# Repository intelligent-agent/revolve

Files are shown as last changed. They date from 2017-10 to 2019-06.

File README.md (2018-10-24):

```
    _/_/_/                                    _/                       
   _/    _/    _/_/    _/      _/    _/_/    _/  _/      _/    _/_/    
  _/_/_/    _/_/_/_/  _/      _/  _/    _/  _/  _/      _/  _/_/_/_/   
 _/    _/  _/          _/  _/    _/    _/  _/    _/  _/    _/          
_/    _/    _/_/_/      _/        _/_/    _/      _/        _/_/_/     
                                                                       
```                                                                      

## Main features
- 1GHz Single board solution using [Octavo OSB3358 SIP](https://octavosystems.com/2016/05/09/osd3358-new-era-integration/)
- 6 [TMC2130](https://www.trinamic.com/products/integrated-circuits/details/tmc2130/) stepper drivers, stall detection, overcurrent/temp
- 4 Thermistor or Thermocouple inputs (runtime configurable)
- 4 high power heater outputs
- 4 GB fast eMMC
- Optionally 2 external drivers
- [Direct coupled PRU lines](http://beagleboard.org/pru) to all drivers
- Flexible PWM on all 8 MOSFET outputs for flexible EMC passing
- 4 USB host ports, 1 USB device port
- 10/100Mbit Ethernet
- 1080p HDMI
- Smart power controls
 - Input voltage and current measurement
 - Power removed detection
 - Software defined overcurrent protecion
- Quad encoder input for filament sensor
- Buffered end stop inputs, ESD protected connectors
- 2 Servo outputs
- Inductive sensor input
- Two Grove connectors, I2C and UART

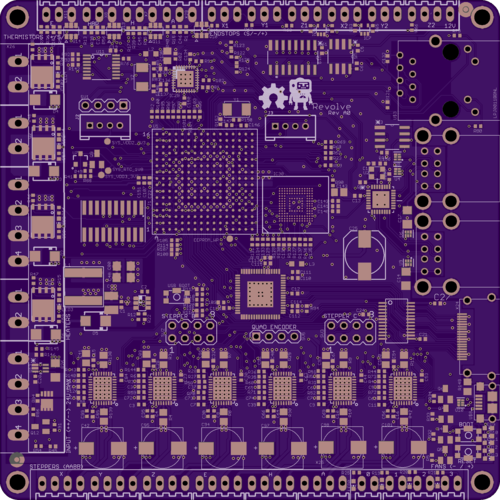
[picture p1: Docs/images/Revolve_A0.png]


## Power management
Here is an overview of the power distribution


## 5V step down TPS54202 calculations

```python
import math
Vout = 5.1 # Output voltage
Vin = 24 # Input voltage
Iout = 2 # Output current
Kind = 0.3 # ?
Fsw = 500000 # Switching frequency
Cbulk = 10 *10**-6
u = 10**6 # micro

```

```python
L=(Vout*(Vin-Vout))/(Vin*Kind*Iout*Fsw)
print "Inductor selection:"
print "Minimum inductor size: "+str(L*10**6)+" uH"

Lout = 15*10**-6
Ilmax = math.sqrt(Iout**2 + (1/12) + ((Vout*(Vin-Vout))/(Vin*Lout*Fsw*0.8))**2)
print "RMS Inductor current "+str(Ilmax)
Ipeak = Iout + (Vout * (Vin - Vout))/(1.6*Vin*Lout*Fsw)
print "Max inductor current "+str(Ipeak)
print "Choosing NR8040T330M"

```

    Inductor selection:
    Minimum inductor size: 13.3875 uH
    RMS Inductor current 2.10904312204
    Max inductor current 2.3346875
    Choosing NR8040T330M

```python
dIout = 0.7
dVout = 0.2 # Delta voltage with dI
Vr = 0.03 # Ripple Voltage
Ir = Iout*0.3
CO1 = (2*dIout)/(Fsw*dVout)
CO2 = (1.0/(8.0*Fsw))*(1.0/(Vr/Ir))
#CO3 =
print "Input Capacitor Selection:"
print "CO1: "+str(CO1*u) + " uF"
print "CO2: "+str(CO2*u) + " uF"

#print "Minimum capacitance: "+str(CO*u)+" uF"
print "Choosing 20uF"
```

    Input Capacitor Selection:
    CO1: 14.0 uF
    CO2: 5.0 uF
    Choosing 20uF

```python
R2 = 100.0*10**3
R3 = 13.3*10**3
Vref = 0.596
Vout = Vref*((R2/R3)+1)
print "Calculation of output resistance: "
print "Vout = "+str(Vout)
```

    Calculation of output resistance:
    Vout = 5.07720300752

## Stepper drivers

Current sense resistor:

```python
R = 0.1
I = 1
U = R*I
P = U*I
print "Power dissipation: "+str(P)
```

    Power dissipation: 0.1

**Diagnostics:**
```python
$2*8 = 16$
```

* Connect together to form a single interrupt?
No, it's good to have individual pins for stallguard.

## Capacitor selection
- 100uF electrolytic capacitor is recommended. No mention of ESR or ripple current in the TMC2130 data sheet.
- What is the frequency at which the largest current draw is expected?
- There are 10uF capacitors in line to handle high frequency current draws, so it is expected that the electrolytic capacitors will handle lower frequecy draws. It depends on cable length, ESR in PSU as well.

**SPI and enable**  
* Enable pins, can it be done using SPI?
* SPI CS pins, need 8 pins at least.
    * Use Mux?
        * Increased cost. How much?
        *
    * Daisy chain?
        * What is the required time?
        * Not good for Stepper A/B. Use CN1?
        * Each transaction takes 60 us
    * Individual pins.
        * Requires 8 pins.
*

```python
print "Stepper readout time: "
a = 6.0*40/(4*10**6)
print "it takes "+str(a*u)+" us for each transaction"
```

    Stepper readout time:
    it takes 60.0 us for each transaction

## PWM calculations

**Current setting**
* Use PWM chip?
    * Costly > $1
    * board space
* Use internal reference
    * 5 bit precision

```python
print "Number of current steps on TMC2130: "+str(2**5)
```

    Number of current steps on TMC2130: 32

# Smart input current monitor circuit.
Fuses have slow responses, so they do not protect against short circuits
and only asymptotically approach their rating with time. They are temperature dependent, difficult to
replace, and physically large. They also increase manufacturing time and cost due to almost universally being
through-hole components.

 - Measure input voltage
 - Measure input current.
 - Choosing PMOS to also implement power lost detection.
 - Reverse polarity protection

```python
R = 0.001
A = 30
adc_vals = 2**12
v_adc = 1.8
v_res = R*A
Gain = 50
resolution =(v_adc/adc_vals)/R/Gain

print "Over current calculations:"
print "Max current: "+str(A)+" A"
print "Resistor value: "+str(R*1000)+" mOhm"
print "Voltage drop across resistor: "+str(v_res*1000)+" mV"
print "Voltage measured: "+str(v_res*Gain)
print "Power dissipation in Rsense: "+str(R*A*A)+" W"
print "resolution: "+str(resolution*1000)+" mA"
```

    Over current calculations:
    Max current: 30 A
    Resistor value: 1.0 mOhm
    Voltage drop across resistor: 30.0 mV
    Voltage measured: 1.5
    Power dissipation in Rsense: 0.9 W
    resolution: 8.7890625 mA

```python
v_max = 24
R1 = 100*10**3
R2 = 4.7*10**3
print "Input voltage calculations: "
print "Voltage divider max output: "+str(v_max*R2/(R1+R2))
print "Input voltage resolution: ??"
```

    Input voltage calculations:
    Voltage divider max output: 1.07736389685
    Input voltage resolution: ??

```python
Imax = 30
RDS = 5.6*10**-3
Ploss = RDS*Imax*Imax
print "Input P-mos power calculations:"
print "Power expenditure: "+str(Ploss)+ " W"
```

    Input P-mos power calculations:
    Power expenditure: 5.04 W

## ESD considerations
 - EN 55024/EN 61000-4-2: ±4kV Contact, ±8kV Air
### Board
 - Ground shield, having 0.1R to ground.
### USB
 - Using [TPD4S012](http://www.ti.com/product/TPD4S012) having Contact: ±10kV, Air: ±10kV
### HDMI
 - Using [TPD12S016](http://www.ti.com/product/TPD12S016)
### Ethernet
 - Isolated using magnetics.
### Endstops
 - Input buffer [CD4050BD](http://www.ti.com/product/CD4050BD) with HBD: ±1500, CDM: ±1000
### Analog
 - Series resistance
### Steppers
 - TMC2130 HBM: ±4 kV
### Heater MOSFETs
 - 4.7nF protection
### Fan MOSFETS
 - No protection

## Layout considerations
Using en562748 as reference for PHY layout.
 - Using 100R resistors in series to reduce EMI.
 - Placing PHY chip close to SIP since differential lines radiate less than 3.3V single ended lines.
 - Removing ground plane under magnetics.
 - 100 Ohm differential impedance
 - Place 49.9ohm pullups close to PHY chip.
 - OSH park uses FR408 laminate

```python
Er = 3.67 # Relative dielectric costant
H = 0.17018 # prepreg height in mm
T = 0.035 # Copper thickness (mm)
F = 125 # Frequency MHz
print "0.15/0.15 track and gap gives 98.4 differential and 65.3 single ended"
```

    0.15/0.15 track and gap gives 98.4 differential and 65.3 single ended

```python
Vf = 2.8 # Diode forward voltage drop (V)
Vin = 3.3 # Input voltage (V)
Vres = Vin-Vf
If = 0.0001 # Diode current, 1mA
R = Vres/If
print "LED power calculations: "
print "Resistor for {}, {}mA: {}".format(Vin, If*1000,R)
```

    LED power calculations:
    Resistor for 3.3, 0.1mA: 5000.0

# Sysboot config
Two Boot modes: MMC1 or USB device
 - SYSBOOT[15-14] = 10b = 25MHz
 - SYSBOOT[13:12] = 00b = reserved
 - SYSBOOT[11:10] = xx
 - SYSBOOT[9] = xx
 - SYSBOOT[8] = xx
 - SYSBOOT[7-6] = xx
 - SYSBOOT[5] = 0b = Disable CLKOUT1
 - SYSBOOT[4:0] = 11100b = MMC1, MMC0, UART0, USB0

 To boot from USB:
 - SYSBOOT[4:0] = 11000b = SPI0, MMCO0, USB0, UART0

```python
Imax = 1.5 # Maximum output current on all 4 USB ports
Rmeas = 0.01 # Current measurement resistor on low side.
RDSon = 0.065 #P-mos RDSon
Vin = 5.1
Vdrop = Vin - (Rmeas + RDSon)*Imax
print "Voltage drop across R: {}".format(Rmeas*Imax)
print "Resulting voltage to USB: {}".format(Vdrop)
```

    Voltage drop across R: 0.015
    Resulting voltage to USB: 4.9875

```python
Imax = 1.5 # Maximum output current on all 4 USB ports
Rmeas = 0.01 # Current measurement resistor on low side.
RDSon = 0.065 #P-mos RDSon
Vin = 5.1
Vdrop = Vin - (Rmeas + RDSon)*Imax
print "Voltage drop across R: {}".format(Rmeas*Imax)
print "Resulting voltage to USB: {}".format(Vdrop)
```

    Voltage drop across R: 0.015
    Resulting voltage to USB: 4.9875

### Review
 - Changed vias to tented
 - Moved pin 1 indicator on U2
 - Moved all test points to top side
 -

```python
from IPython.display import display, Markdown, Latex
```

## Calculation of power dissipation of P-MOS
* `$R_{ds(on)max} = 45 m\Omega$ @ $-10 V$`
* Thermal Resistance, Junction to Ambient @ `$TA=+25 ^{\circ}C$ is $R_{\theta JA}=26 ^{\circ}C/W$`

```python
Von=6
Ta=25
Imax=30
#Imax=2
Rdson=0.0045
TR=26

# P=I^2*R
P=Imax*Imax*Rdson

Trise=TR*P
T=Ta+Trise

display(Markdown("""
$P={P:0.3f} W$\n
$T_{{rise}} = {Trise} ^{{\circ}}C$\n
$T = T_A + T_{{rise}} = {T:0.3f} ^{{\circ}}C$ when $I={I:.0f} A$

""".format(P=P, Trise=Trise, T=T, I=Imax)))
```

    $P=4.050 W$

    $T_{rise} = 105.3 ^{\circ}C$

    $T = T_A + T_{rise} = 130.300 ^{\circ}C$ when $I=30 A$

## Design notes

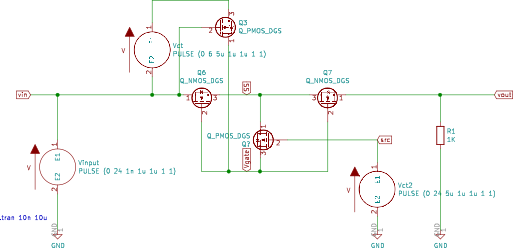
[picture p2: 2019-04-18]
PCB/Revolve_A5/img/schematic.png

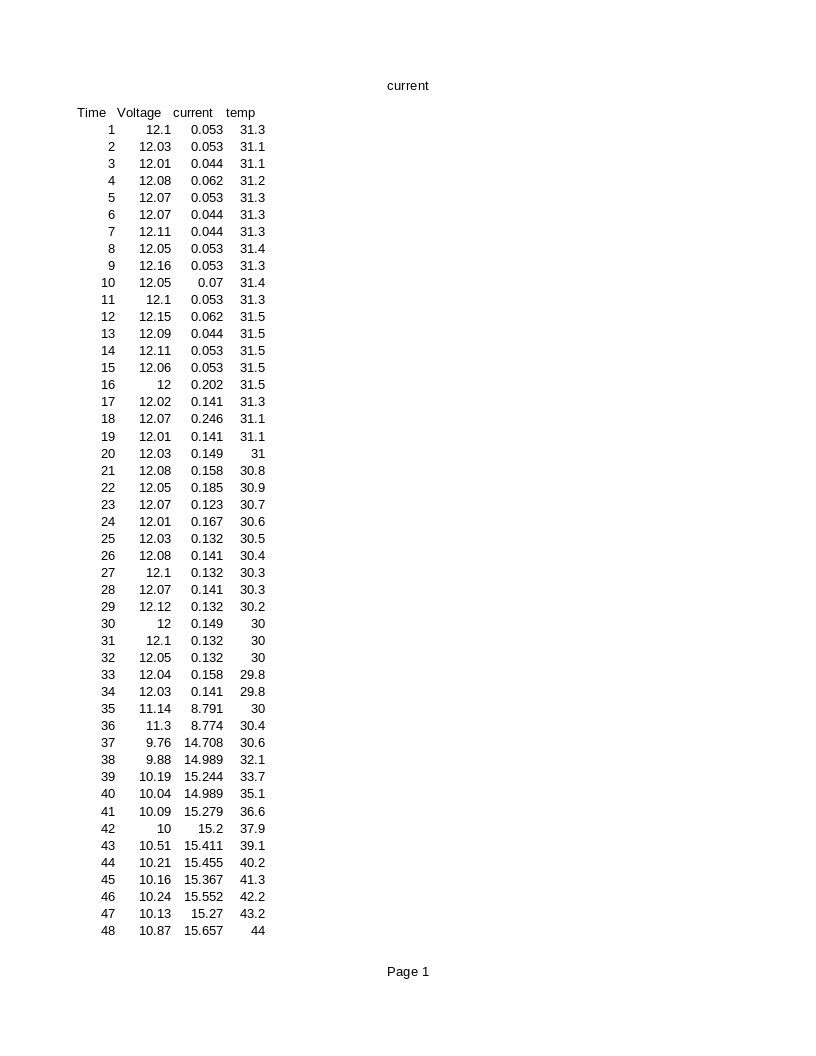
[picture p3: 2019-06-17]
PCB/Revolve_A5/img/current_15A_fan.png

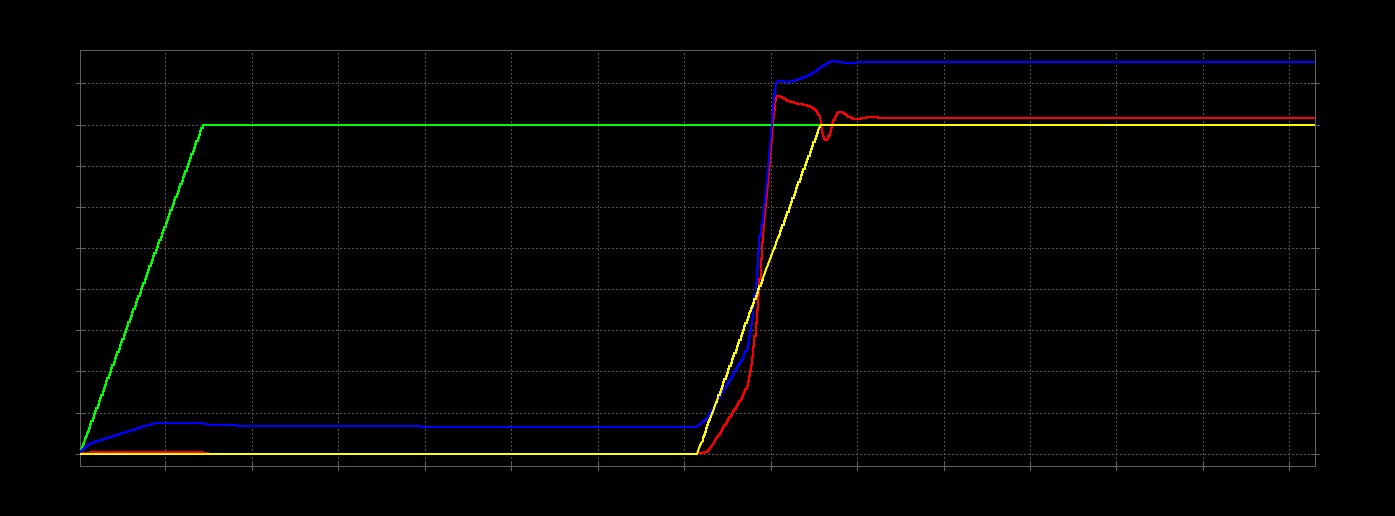
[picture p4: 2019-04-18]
PCB/Revolve_A5/img/simulation_nmos_1R-load.png

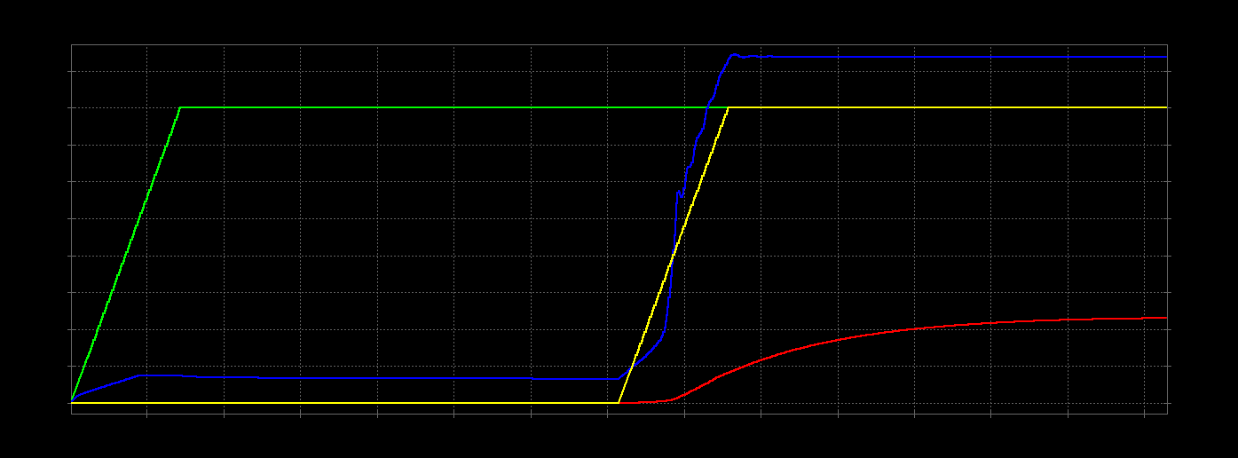
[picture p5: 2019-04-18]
PCB/Revolve_A5/img/simulation_nmos_1m-load.png

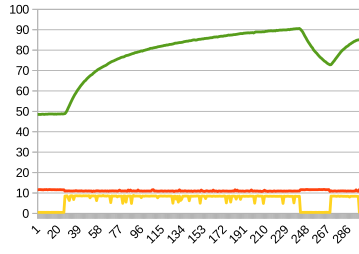
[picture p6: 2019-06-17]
PCB/Revolve_A5/img/current.png

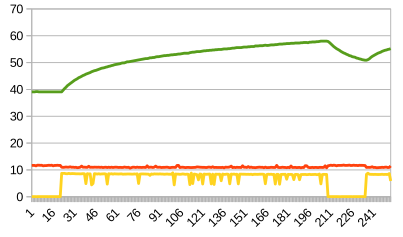
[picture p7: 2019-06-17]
PCB/Revolve_A5/img/current_new_2.png

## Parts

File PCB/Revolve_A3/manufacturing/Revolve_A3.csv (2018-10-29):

Qty | Value | Device | Package | Parts | Description | MPN | Notes
1 |  | CTI-JTAG | CTI-JTAG | J1 |  |  | DNP
2 |  | MA04-1 | MA04-1 | SV1, SV5 | PIN HEADER |  | DNP
2 |  | MA05-2 | MA05-2 | SV4, SV6 | PIN HEADER |  | DNP
5 |  | NPN-TRANSISTOR_SOT23 | SOT23 | Q4, Q5, Q6, Q7, Q12 | NPN TRANSISTOR | AO7400
1 | 0.001,1% | R-EU_R1206 | R1206 | R26 | RESISTOR, European symbol | CSR1206-0R001F1
13 | 0.1R | R-EU_R0805 | R0805 | R3, R4, R7, R8, R9, R10, R11, R29, R30, R42, R138, R139, R149 | RESISTOR, European symbol | RL1220S-R10-F
61 | 0.1uF | C-EUC0402 | C0402 | C1, C2, C4, C5, C6, C8, C10, C12, C13, C15, C16, C18, C19, C20, C21, C23, C24, C27, C28, C29, C30, C31, C35, C38, C40, C43, C44, C53, C54, C56, C60, C61, C63, C64, C66, C67, C69, C70, C72, C73, C74, C82, C83, C84, C85, C87, C99, C107, C108, C110, C114, C115, C133, C134, C138, C140, C141, C142, C150, C151, C155 | CAPACITOR, European symbol | CL10B104KB8NNND
1 | 0.1uF | C-EUC0402 | C0402 | C32 | CAPACITOR, European symbol | CL10B104KB8NNND
1 | 10,1% | R-EU_R0402 | R0402 | R83 | RESISTOR, European symbol | RC0402FR-0710RL
15 | 100 | R-EU_R0402 | R0402 | R85, R95, R96, R97, R98, R99, R100, R101, R102, R103, R104, R161, R162, R180, R181 | RESISTOR, European symbol | RC0402FR-07100RL
19 | 100K,1% | R-EU_R0402 | R0402 | R12, R45, R87, R105, R107, R108, R114, R115, R116, R117, R118, R119, R120, R174, R175, R176, R177, R178, R179 | RESISTOR, European symbol | RC0402FR-07100KL
1 | 100K,1% | R-EU_R0402 | R0402 | R84 | RESISTOR, European symbol | RC0402FR-07100KL
1 | 100uF | CPOL-EU153CLV-0605 | 153CLV-0605 | C25 | POLARIZED CAPACITOR, European symbol | RSL0J101MCN1GB
6 | 100uF,35V,0.025R | C | RHS1V10MCN1GS | C42, C94, C95, C97, C98, C101 |  | RHS1V101MCN1GS
39 | 10K,1% | R-EU_R0402 | R0402 | R1, R2, R6, R27, R31, R35, R37, R38, R39, R40, R43, R50, R55, R56, R57, R58, R60, R73, R78, R81, R88, R90, R94, R121, R127, R128, R129, R130, R131, R132, R133, R134, R135, R136, R137, R140, R141, R147, R152 | RESISTOR, European symbol | RC0402FR-0710KL
2 | 10uF,3.3V | C-EUC0805 | C0805 | C135, C143 | CAPACITOR, European symbol | C0805C106K8PACTU
7 | 10uF,35V | C-EUC0805 | C0805 | C41, C47, C89, C91, C92, C93, C100 | CAPACITOR, European symbol | GMK325BJ106MN-T | Alternative component: GRM21BR6YA106KE43K
1 | 12.1K, 1% | R-EU_R0402 | R0402 | R82 | RESISTOR, European symbol | RC0402FR-0712K1L
1 | 13.3K,1% | R-EU_R0402 | R0402 | R22 | RESISTOR, European symbol | RC0402FR-0713K3L
2 | 150OHM,800mA | L-USL2012C | L2012C | L2, L3 | INDUCTOR, American symbol | MU2029-151Y
1 | 15uH | RT8040T330 | NR8040T330 | L1 |  | NRS8040T150MJGJ
7 | 18pF | C-EUC0402 | C0402 | C36, C146, C147, C148, C149, C156, C157 | CAPACITOR, European symbol | GRM0335C1E180JA01D
1 | 1K,1% | R-EU_R0402 | R0402 | R53 | RESISTOR, European symbol | RC0402FR-071KL
7 | 1K,1% | R-EU_R0402 | R0402 | R106, R109, R110, R111, R153, R154, R155 | RESISTOR, European symbol | RC0402FR-071KL
1 | 1M | R-EU_R0402 | R0402 | R150 | RESISTOR, European symbol | RC0402JR-071ML
6 | 2.2R | R-EU_R0402 | R0402 | R52, R59, R70, R71, R72, R126 | RESISTOR, European symbol | RC0402FR-072R2L
5 | 2.2uF | C-EUC0402 | C0402 | C34, C109, C111, C112, C113 | CAPACITOR, European symbol | GRM155R61A225KE95D
4 | 22-05-7028-02 | 22-05-7028-02 | 7395-02 | X4, X5, X6, X9 | CONNECTOR | 640455-2
9 | 22-05-7038-03 | 22-05-7038-03 | 7395-03 | X1, X7, X8, X10, X11, X13, X19, X22, X29 | CONNECTOR | 640455-3
7 | 22-05-7048-04 | 22-05-7048-04 | 7395-04 | X12, X14, X15, X16, X17, X18, X25 | CONNECTOR | 640455-4
7 | 22nF | C-EUC0402 | C0402 | C3, C7, C9, C11, C39, C88, C132 | CAPACITOR, European symbol | C1005X7R1E223K050BB
4 | 22uF | C-EUC1206 | C1206 | C14, C17, C48, C80 | CAPACITOR, European symbol | CL31B106KAHNNNE
2 | 25MHz | 445C33D24M00000SMALL | 445C33D24M00000 | Y1, Y2 |  | 445C33D25M00000
49 | 4.7K,1% | R-EU_R0402 | R0402 | R5, R13, R14, R15, R16, R17, R18, R19, R20, R21, R23, R24, R25, R28, R32, R33, R34, R36, R44, R46, R47, R48, R51, R54, R61, R62, R63, R64, R65, R66, R67, R68, R69, R74, R75, R76, R77, R89, R91, R92, R93, R112, R142, R143, R144, R145, R171, R172, R173 | RESISTOR, European symbol | RC0402FR-074K7L
5 | 4.7nF | C-EUC0402 | C0402 | C22, C57, C58, C59, C102 | CAPACITOR, European symbol | CL05B472KA5NNNC
11 | 4.7uF | C-EUC0402 | C0402 | C26, C33, C37, C45, C46, C49, C55, C65, C68, C86, C103 | CAPACITOR, European symbol | GRM155R60J475ME47D
3 | 40.2K,1% | R-EU_R0402 | R0402 | R41, R86, R148 | RESISTOR, European symbol | RC0402FR-0740K2L
1 | 445C33D24M000003.2X2.5 | 445C33D24M000003.2X2.5 | 403C35E12M00000 | U$22 |  | ABM8G-12.000MHZ-4Y-T3
2 | 470 | R-EU_R0402 | R0402 | R79, R80 | RESISTOR, European symbol | RC0402JR-07470RL
1 | 470pF | C-EUC0402 | C0402 | C136 | CAPACITOR, European symbol | CL05B471KB5NNNC
1 | 47k,NTC | R-EU_R0402 | R0402 | R146 | RESISTOR, European symbol | NCP15WB473E03RC
4 | 49.9,1% | R-EU_R0402 | R0402 | R122, R123, R124, R125 | RESISTOR, European symbol | RC0402FR-0749R9L
1 | 499 | R-EU_R0402 | R0402 | R49 | RESISTOR, European symbol | RC0402FR-07499RL
2 | 4P-2.0 | GROVE-CONNECTOR-DIP(4P-2.0) | HW4-2.0 | J2, J3 | 320110033 | 1125S-4P
1 | 649,1% | R-EU_R0402 | R0402 | R113 | RESISTOR, European symbol | RC0402FR-07649RL
3 | 74AHC1G126DCK | 74AHC1G126DCK | SC70-5 | IC1, IC6, IC7 | Single Bus Buffer Gate With 3-State Outputs | M74VHC1GT126DF1G
4 | AON6758 | AON6758 | 8-DFN-EP-(5X6) | Q1, Q2, Q3, Q8 |  | SIRA34DP-T1-GE3
1 | APX811SOT | APX811SOT | SOT143-R | U12 | Diodes APX811/812 4-pin Microprocessor Supervisor with Manual Reset. | APX811-31UG-7
1 | CD4050BD | CD4050BD | SOIC127P600X175-16N | U19 | CMOS Hex Buffer/Converters | CD4050BDR
1 | CY7C65632 | CY7C65632 | QFN28 | IC2 | CY7C65632 edit this description | CY7C65632-28LTXCT
4 | DMC2038LVT | DMC2038LVT | TSOT26 | Q10, Q11, Q13, Q14 |  | DMC2038LVT-7
1 | HDMI4 | HDMI4 | HDMI-A-TH | X24 |  | 609-4614-2-ND
1 | INA199A1DCKR | INA199A1DCKR | SOT65P210X110-6N | U13 | CURRENT SHUNT MONITOR | INA199A1DCKR
1 | LAN8710A | LAN8710A | 32-QFN | IC29 | LAN8710A edit this description | LAN8710A-EZC-TR
1 | LPJ0011BBNL | LPJ0011BBNL | LPJ0011BBNL | U$3 |  | LPJ0011BBNL
5 | MBRA340T3 | MBRA340T3 | SMA | D1, D2, D3, D4, D5 | Surface Mount Schottky Power Rectifier | MBRA340T3G
1 | MMBT2907 | MMBT2907SMD | SOT23-BEC | Q9 | PNP Transistror | MMBT2907ALT3G
3 | MSTBA2 | MSTBA2 | MSTBA2 | X3, X21, X26 | PHOENIX | 39532-1002
2 | MSTBA4 | MSTBA4 | MSTBA4 | X2, X20 | PHOENIX | 39532-1004
1 | MTFC2GMDEA | MTFC2GMDEA | WFBGA | IC30 | MTFC2GMDEA edit this description | EMMC04G-M627-X03R
1 | OSD3358-512M-BSM | OSD3358-512M-BSM | OSD335X-BGA-256 | U1 | Octavo Systems LLC OSD335x Family SiP: 21mm x 21mm, 1.27mm pitch 256 pin BGA contains AM3358, 512MB DDR3, TPS65217, TL5209, EEPROM and passives. Commerical Temperature: 0C to 85C. | OSD3358-512M-BSM
2 | SISS27DN | SISS27DN | POWERPAK-1212-8S | U$11, U$17 |  | SISS27DN-T1-GE3
1 | SN74AHC595PW | SN74AHC595PW | SOP65P640X120-16N | U11 | 8 bit shift registers with 3-state output registers | SN74AHC595PW
3 | TACT_SWITCH | TACT_SWITCH | DHT-1147 | U$19, U$20, U$21 |  | DHT-1147
1 | TDA19988BHN/C1,557 | TDA19988BHN/C1,557 | SOT804-4 | U$7 |  | TDA19988BHN/C1,518
1 | TLVH431 | TLVH431 | SOT23-3 | U7 |  | TLVH431IDBZR
1 | TPD12S016-RKT | TPD12S016-RKT | R-PDSO-G24 | U$18 |  | TPD12S016PWR
5 | TPD4S012_DRY_6_P1_P | TPD4S012_DRY_6_P1_P | DRY6 | U4, U6, U8, U9, U10 |  | TPD4S012DRYR
1 | TPS2061D | TPS2061D | SOIC127P600X175-8N | U3 | CURRENT-LIMITED, POWER-DISTRIBUTION SWITCHES | TPS2061D
1 | TPS54202 | TPS54202 | SOT23 | U$10 |  | TPS54202DDCR
6 | TRINAMIC_TMC2130_QFN36 | TRINAMIC_TMC2130_QFN36 | TRINAMIC_QFN36 | U$2, U$9, U$13, U$14, U$15, U$16 |  | TMC2130-LA-T
1 | UA78L05ACD | UA78L05ACD | SOIC127P600X175-8N | U5 | POSITIVE-VOLTAGE REGULATORS | UA78L12ACDR
2 | USB-A | USB-A | USB-A | U$5, U$6 |  | 320010475
1 | USB-MICRO | USB-MICRO | USB-MICRO | U$8 |  | ST-USB-001G-4
14 | blue | LEDCHIP-LED0603 | CHIP-LED0603 | LED0, LED1, LED2, LED3, LED4, LED5, LED6, LED7, LED8, LED9, LED10, LED11, LED12, LED13 | LED | 19-217/BHC-ZL1M2RY/3T

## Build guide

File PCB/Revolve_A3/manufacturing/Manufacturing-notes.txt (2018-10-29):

Production notes: 
- Solder mask: Black matte
- Silk screen: White
- Final height: 1.6 mm
- Final finish: ENIG
- Base material: FR4
- Final outer layer copper thickness: 35 um
- Material Tg: Min 130 deg C

Conductive layer stackup: 
- CMP
- LY2
- L15
- SOL

Impedance: 
The impedance of the coupled microstrip line is based on: 
Er of 3.6 and a hight from top to first inner layer of 0.19 mm 
to achieve a 90 ohm diffrential impedance. 
Any deviations from this might require re-routing or re-calculation.

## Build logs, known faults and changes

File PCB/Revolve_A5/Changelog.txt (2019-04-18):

Changelog from rev A3 to A5

TODO: 
-----
 - Consider protection from reverse current from steppers. 

DONE:
-----
 + Converted from Eagle 6 to KiCad 5.1
 + Better thermal design on input

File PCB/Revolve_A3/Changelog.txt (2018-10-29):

Changelog from rev A2 to A3

TODO: 
-----
 + Change AP811 from 46 to 31. (Wrong monitoring voltage)
 + Clean up silk screen

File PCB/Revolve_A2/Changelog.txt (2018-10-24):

TODO: 
-----
 + missing 5V on USB_VBUS might prevent USB from working in U-boot/Kernel (Switched USB_VBUS to SYS_5V)
 + Missing 1.5K pull-up on USB1_DP (Not needed for new USB hub)
 + USB hub is Full-speed. Change to High speed. 
 + mmc1: switch to bus width 8 failed (No longer routed through A6)
 - Heater E not working. (Probably a software problem.)
 + Consider output voltage on external drivers. (added 3.3 and 24V)

Stuff that is working:
 - All PWMs/timers are working so we have 4 heaters + 4 fans. (Not Heater E, might be a software problem)
 - As far as I can tell, the current, voltage and temperature sense on the input is OK, 
but perhaps not enough time to store position if power is lost. It depends on well we can integrate power managent into the Cortex M3 core on the board. 
 - The HDMI output is OK. 
 - USB hub works but is only 12 Mbps
 - Ethernet works
 - USB device works
 - Thermistor inputs.
 - Endstops
 - Thermocouple inputs
 - Steppers!
 - Rotary encoder. 
 - Wifi 

Not working yet:
 - 8 bit eMMC
 - Grove connectors (One I2C, one UART
 - Servos not yet tested. 
 - External stepper drivers

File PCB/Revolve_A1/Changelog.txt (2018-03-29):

TODO: 
-----
 - 
 + Change 10.000 pF to 0.1uF (This was right in the schematic, but seems to have been changed during ordering)
 + Change footprint on Y4
 + Consider dropping 2.2uF (Dropped 1uF, cutting one bom-line)
 + 0201 package on the 18pF caps in the BoM
 + Change 10V 0805 10uF caps to 35V (Where is this? The MPN in schematic is right) 
    + Wrong voltage on 10uF for steppers (PartNo in schemtic is wrong). Use MPN
 + Smaller footprint on C25 (Changed to 6.3mm diameter)
 + Change SOT23 footprints
 + TPD12S01 wrong package in the BoM: (Changed SPN in the schematic)
 + U5 is 5V, should be 12V (changed MPN and SPN)
 + HDMI footprint slightly to the side. 
 + Use the large test points, gather them and place on one side. 
 + Connect USB HUB pin 27 to gnd. (TSTPLL)
 + Ethernet connector wrong footprint 
 + missing pull-up on OC pin 5V usb. 
 + Missing pull-up on USB0_DP ( Not adding pull-up, reference design does not have it. )
 + Missing solder paste on eMMC
 + Mising reset pin on eMMC
 + EP (GND pad) on USB hub not connected to GND. 
 + C20 seems to have blown up.... (It has 3.3V across it, so it seems random)
 + GANGED pin must be pulled high on the USB hub. 
 + Add 22R + 15K pull-downs + caps on transmission lines for the USB. (Dropped Caps, bit otherwise OK)
 + Move Fan LEDs to 3.3V line instead of 24V line. Too bright. 
 + Consider adding an LED to indicate 12/24V is enabled. (Added LED on enable wire)
 + More room around the PMOS chips on the input. (Added tPlace)
 + Move LEDs to make room for connectors. (switched USB device and LEDS)
 + Consider C6-75pF for loop stability on TPS54202 (Added a C6 of 18pF. Can be increased if needed)
 + Change PMIC_PGOOD to be Push/pull compatible.
    ( Using a buffer with an enable input ) 
 + USB1_VBUS connected to SYS_5V. (Conected USB1_VBUS to USB_VBUS)
 + No low voltage tracks under the inductor. Makes noise. (Rerouted out of the way)
 + Missing 1.8V on VDDDC1 and 2 on HDMI 
 + Consider ferrite beads on analog domain.  (Contained in the SiP?)
 + Consider removing diag 1
    (No need to remove it, the design works now)
 + Pin 9 on TMC2130 floating. 
 + Resistors on gates. (Added 100R resistors on high power mosfets to aid in ringing (LC) and current draw.)
 + Move USB and HDMI further apart (Added an indicator for 20mm)
 + Thermistor markings wrong
 + Much noise on the thermistors. Fix layout to reduce noise level. Currently it's 30 mV PP
    (Moved filter closer to SiP input and connected VREFN to AGND_ADC)
 + Remove clkout_25MHz
 + SISS27DN add outline 

 From Octavo:
 + Silk screen errors: (Component names will not be on final board. )
 + Rename +3V3 to sys_vdd1_3v3
 + Make R49 499ohm
 + Fix JTAG header connections
    + TVDD is not pulled high.
    + TCLKRTN is not connected to TCK.
    + EMU0 and EMU1 are not pulled high.
    + JTAG_TRSTN is not pulled low.
    + TDIS is not grounded.
 + Change eMMC pull-ups to 10K. 
 + PMIC_MUX connected to PMIC_MUX_OUT on the SiP
 + Complete top and bottom side ESD ring
 + Remove thermal pour on L1
 + Widen VIN_AC pour
 + Check traces (24V and 12V) for U5: (Max 150mA, so should be OK)
 + Remove VIN_BAT pour. 
 + Increased the traces for the clamping circuit to 0.3 mm (12mil) 
 + Update the PWRONRSTN / WARMRSTN schematic
 + Consider 1.5K resistor on LEDs: (The LEDs are bright enough with 4.7K) 
 + 5.1) Pull Don't care bits to GND. 
 + 5.2) Not adding a 100R resistor due to board space. 
 + 5.4) Make eMMC compatible with V5.0 (Not possible since DAT6 is surrounded on all sides. )
 + 8.1) Connect VREFN to AGND_ADC
 + 8.2) Fixed PMIC_MUX signal is not correct. 
 + 8.3) You might want to change R68, R67 R23 and R69 to 1.5K resistors to improve the brightness of the LEDs. (They are bright enough)
 + Check signals for 90 degree turns
 + Check copper pours for small areas. 
 + Using 4 vias on USB_DC copper pour

From Seeed: 
 + New USB host connectors (Same footprint)
 + New tactile sitches (New foorprint)
 + New capacitors (Same footprint)
 + New edge headers (Same footprint)

Stuff that is working:
 - All PWMs/timers are working so we have 4 heaters + 4 fans. 
 - As far as I can tell, the current, voltage and temperature sense on the input is OK, 
but perhaps not enough time to store position if power is lost. It depends on well we can integrate power managent into the Cortex M3 core on the board. 
 - The HDMI output is OK. 
 - USB hub works with some workarounds. 
 - Ethernet works
 - USB device works
 - Thermistor inputs.
 - Endstops, all but Y1 seems to be working
 - Thermocouple inputs
 - Steppers!

Not working yet:
 - Grove connectors (One I2C, one UART)
 - Servos not yet tested. 
 - Rotary encoder.  
 - External stepper drivers

Board bring-up: 
 - Measured all voltage domains, no shorts. 
 - Applied USB power, no message in kernel. 
 - 3.315V on VDD2
 - 3.339 on VDD3
 - 1.113 on VDD_FPU
 - 1.808 on VDD_RTC
 - 4.95 on SYS_5V
 - 1.807 on VDD_PLL 
 - 1.04 on VDD_CORE
 - 1.40 on VDDS_DDR

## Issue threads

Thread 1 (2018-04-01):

Connectors for Steppers should be type XH or Dupont not tyco  MTA and also straight not 90 degrees

dembach, 2018-04-01:
since Stepper Drivers have got XH 6 pin connectors and there are two types of cables , but none of them are using tyco MTA.
here are the corresponding pictures:
Stepper connector XH , with securing...:
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
Connector Dupont, does not have securing , jut like a jumper.
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
and the never beeing used MTA, with securing , compatible with dupont but without securing:
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

Also the footprint is getting bigger using 90 degree connectors.
just use the straight ones ....

raykholo, 2018-04-05:
I have plenty of stepper motors with dupont connector and this is not secure in XH - the male pins of XH are too short to firmly hold female dupont.

AcrimoniousMirth, 2018-05-02:
I've used XH on my GT2560 and Dupont on the RAMPS. While the idea of XH is nice I'm personally a fan of Dupont. They're way more accessible, can be rotated to invert motor direction (useful for setup) and I've never had any issues with them working their way loose.
I can see where XH is more useful in ensuring polarity but if you're splashing out for a Revolve board there's a good chance you're not going to be stupid enough to make that mistake anyway.

AaronHerrick, 2019-11-16:
Use whatever connector floats your boat, dupone, XH, whatever.  But having the pins out at 90 degrees makes it harder to plug in, given that boards are usually accessible in only 1 direction (up) and increases the possibility of shorting unused connections.

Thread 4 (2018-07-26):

Is this project dead?

npgoalkeeper, 2018-07-26:
I see that the files haven't been updated for over 4 months now. Is the project dead?

eliasbakken, 2018-07-26:
Not at all, but there have been some delays due to the delivery of the
previous Kickstarter and making the pre production batch. I made a board a
couple of days ago to get started with making a testing jig for it.

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

marcboivin, 2018-08-10:
Glad to hear it. Good luck with the progress. Can't wait to get my hand on one!

Closed 2018-09-14.

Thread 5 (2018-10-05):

Any updates?

LazaroFilm, 2018-10-05:
Any updates on this project? An estimated release date?
Also will you be able to use [Klipper](https://github.com/KevinOConnor/klipper) on this? This seems to be the perfect platform for it.

AcrimoniousMirth, 2018-11-30:
Seconded.

Casey7747, 2019-05-18:
Third-ed. This is an amazing controller that I would love to implement in my new printer. When can we expect a saleable release?

eliasbakken, 2019-05-20:
Sorry that this is taking so long. It's way over due with an update and I
don't mean to string anyone along. Its not clear how much longer it will
take, perhaps months since we still have to do CE and FCC before releasing
the final board. To give a preview of what is going on, 10 boards have been
made for software developers, but there was an issue with the input stage
causing the board to become too hot at high currents. A new revision has
been made, but it needs to be tested and then we need to do a small batch
to do CE/FCC. If the tests go well we still need some time to finalize the
flashing and testing jigs and then start the 30 days pre order.

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

DocTrucker, 2019-05-22:
Been looking around for a second platform to use alongside Duets and this is interesting. Does it support PT100 sensors either directly or through daughter boards? Is it likely that two boards could sync together to get more steppers? Max step rate to 6 drives? Heater fault detection/protection?

eliasbakken, 2019-05-22:
PT100 is supported through an external PT100 amplifier board, which is the
right way to do it.
You can not sync multiple boards with the same accuracy as the steppers
have between them. I don't know of any board that can do that though.
There are 6 internal steppers with two external steppers as well as an
addition. Max step rate to all synchronously.
Heater fault detection is a software issue more than a hardware issue I
would say. For details on that, please refer to the Redeem project.

Kind regards,
-Elias

ons. 22. mai 2019 kl. 08:13 skrev DocTrucker <notifications@github.com>:

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

DocTrucker, 2019-05-29:
Thanks for taking the time to respond.

Casey7747, 2019-07-04:
Hey DocTrucker,
Both of those are PT100 suitable boards. Not sure what you mean by fake a thermistor so I'll say this.

**Adafruit**
-2/3/4 wire PT100
-SPI Comms output. You will need to confirm that Elias has made SPI connections available. (Nothing mentioned on the main page. I might check tonight if I can see them on the PCB)
-May need additional programming, but not too much, to communicate with Revolve.
-This is a higher quality design unit compared to the other.
-https://www.adafruit.com/product/3328

**E3D Online**
-2 wire PT100 (3/4 wire probe will still work but the system is generally less accurate.)
-Analog Output(0-5V), needs to be connected to an analog input pin. ou will need to confirm that Elias has made analog input connections available. (Probably has, I might check tonight if I can see them on the PCB)
-https://e3d-online.com/pt100-amplifier-board

Hope this helps

Felix

DieKatzchen, 2019-11-30:
How goes the CE/FCC testing? Any updates?

eliasbakken, 2019-12-01:
@DieKatzchen the project is cancelled and replaced by Recore: http://www.thing-printer.com/recore/

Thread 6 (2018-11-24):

Is there a power loss pause/resume  feature implemented?

amrithmmh, 2018-11-24:
so i saw power loss detection feature in the list of features so can this board detect power loss and save the print and resume once power is on?

amrithmmh, 2018-11-24:
also what is the update on this board and firmware i am eagerly waiting for it come to market

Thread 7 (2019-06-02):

CAN Bus support

moritzmhmk, 2019-06-02:
With CAN-FD based Extension boards being planned for the Duet3d v3 it might be a good idea to have that option with the revolve as well - especially since the beagle has native support and only a transceiver needs to be added to the board.

In case this issue is to late for changes to the board: are the pins accessable so one could ad a transceiver on an extra board?

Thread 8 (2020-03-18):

Wrong symbol presentation for Q16 (DMC2038LVT) at power in (ENABLE_STUFF)

wmzart, 2020-03-18:
After looking at the power input circuit, I found that the presentation of the n_channel mosfet symbol has the gate and the drain swapped. The pin name and numbers are correct but the schematic representation is wrong.

The ENABLE_STUFF is an output pin from from the OSD3358 (USB0_DRVVBUS) and should drive gate1 at Q16. Furthermore, drain1 at Q16 should be able to pull gate2 at Q16 down. Otherwise it doesn't make sense.

Also, according to the manufacturer diodes.com, the DMC2038LVT is not recommended for new design. They recommended to use their successor: DMC2053UVT

wmzart, 2020-03-18:
Revolve has a successor: Recore. See here http://www.thing-printer.com/recore/

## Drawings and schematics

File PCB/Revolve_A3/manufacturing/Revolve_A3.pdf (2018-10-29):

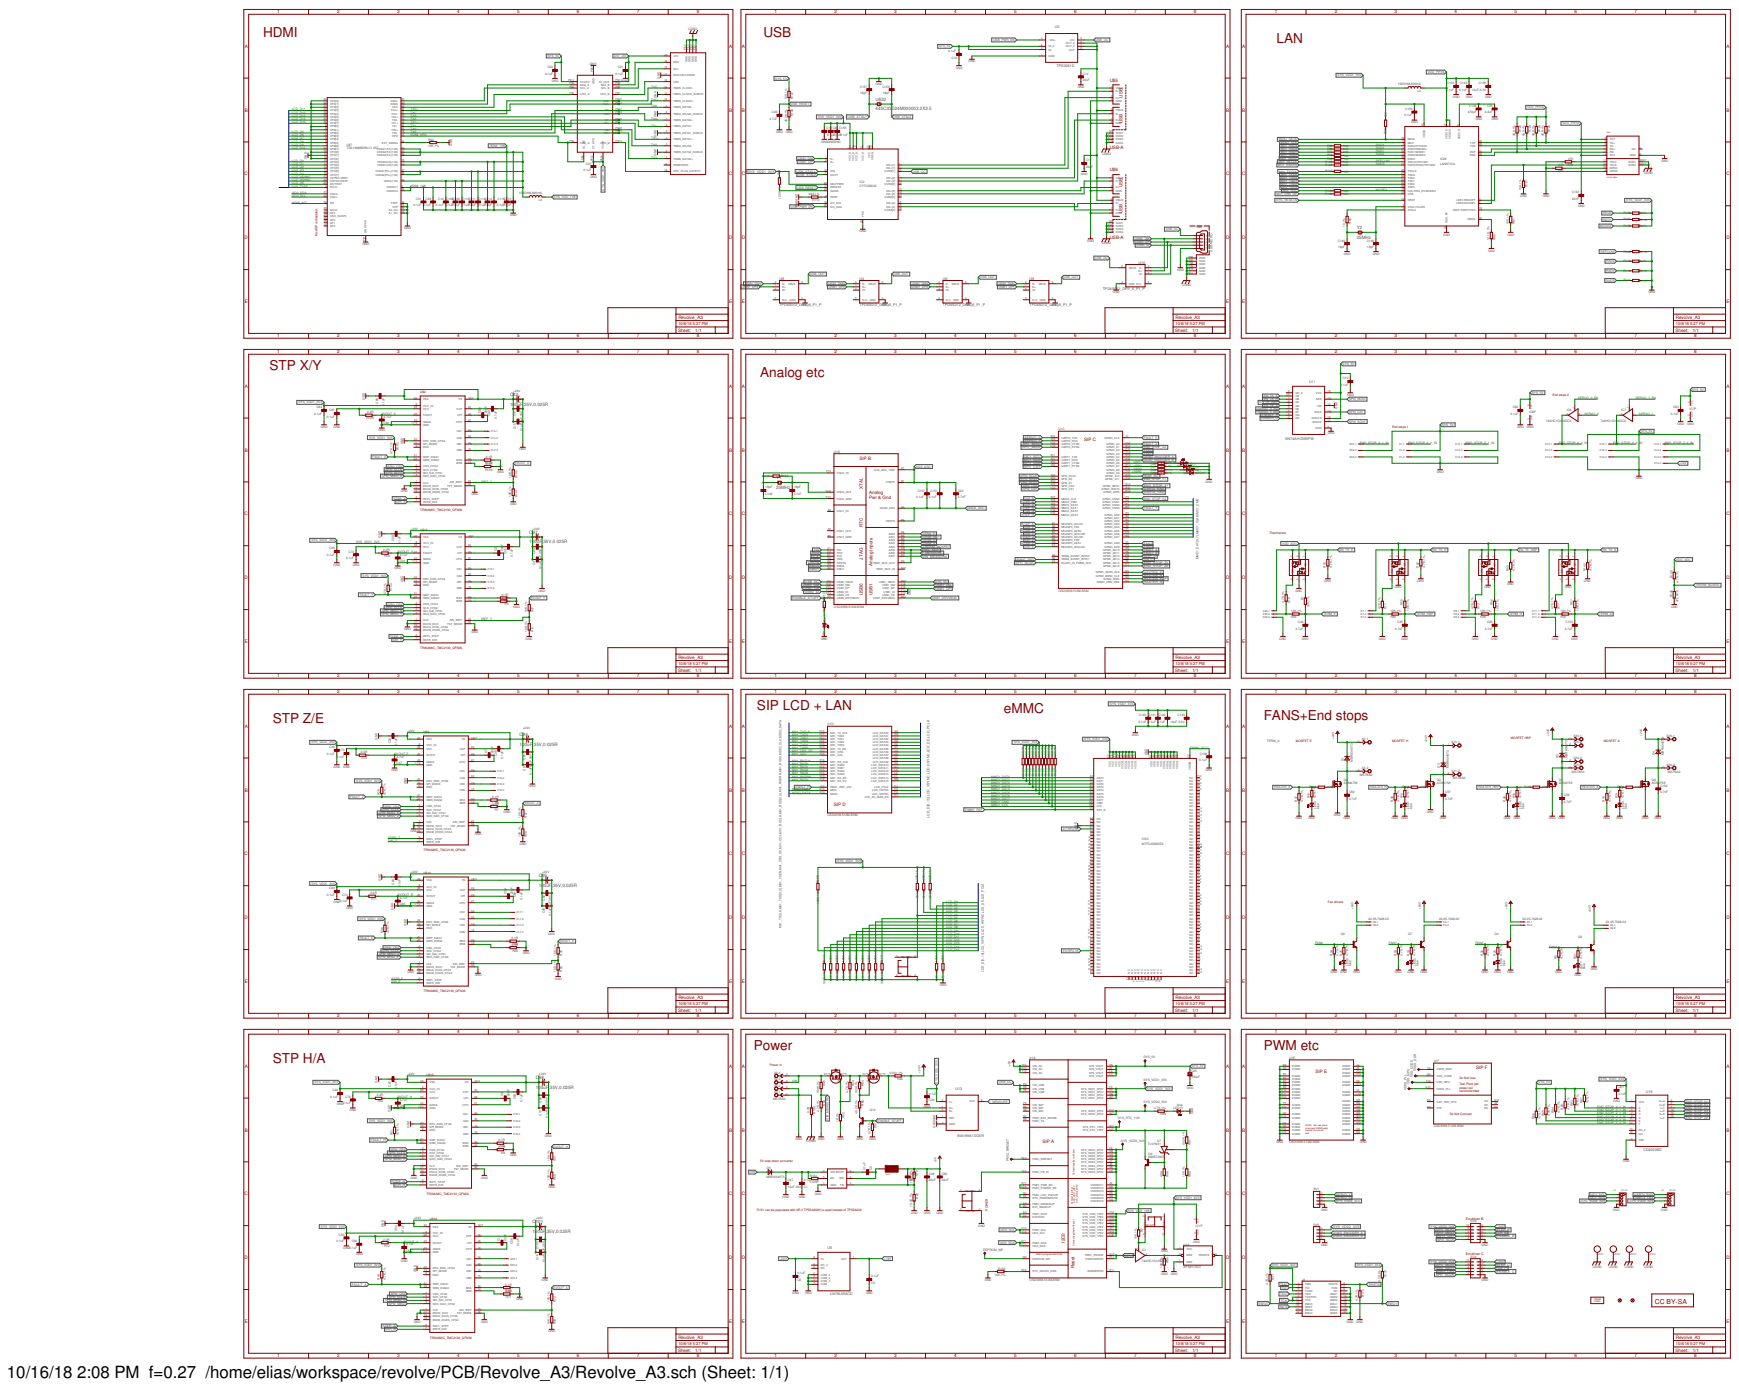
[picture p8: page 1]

GND GND

F14 NC G1 NC G2 NC G3 VSS G5 NC G10 NC G12

Do Not Use Test Point per power rail recommended

NOTE: Can use pours
to connect DGND pads
instead of a via per pad.

SYS_VDD3_3P3V Connect together with pour Connect together with pour

I2C0 Reset Connect to either: SYS_VDD_1P8V

R151 can be populated with 0R if TPS54202H is used instead of TPS54202

GND to program EEPROM

10/16/18 2:08 PM f=0.27 /home/elias/workspace/revolve/PCB/Revolve_A3/Revolve_A3.sch (Sheet: 1/1)

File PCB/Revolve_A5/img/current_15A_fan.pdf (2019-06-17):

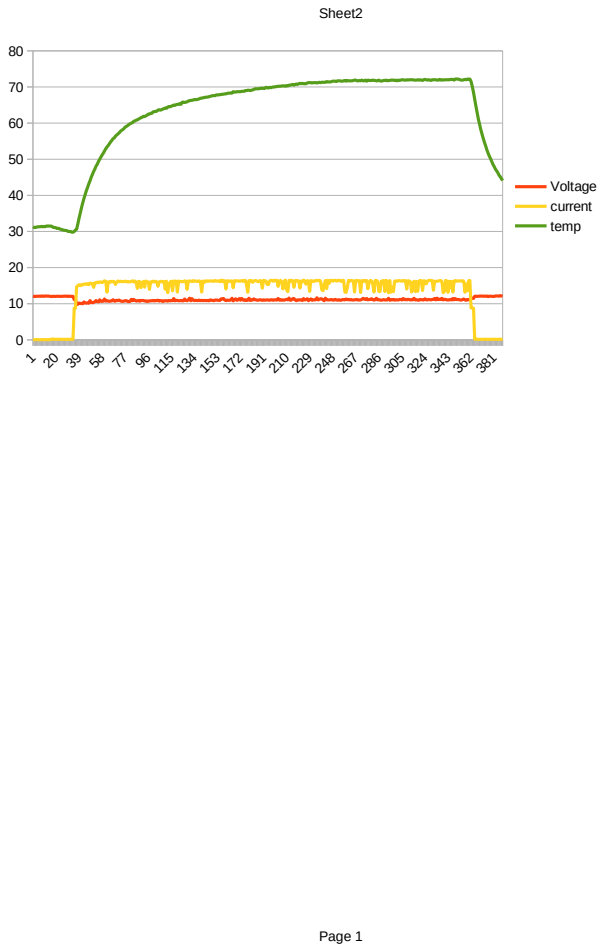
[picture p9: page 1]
Sheet2; Voltage current temp

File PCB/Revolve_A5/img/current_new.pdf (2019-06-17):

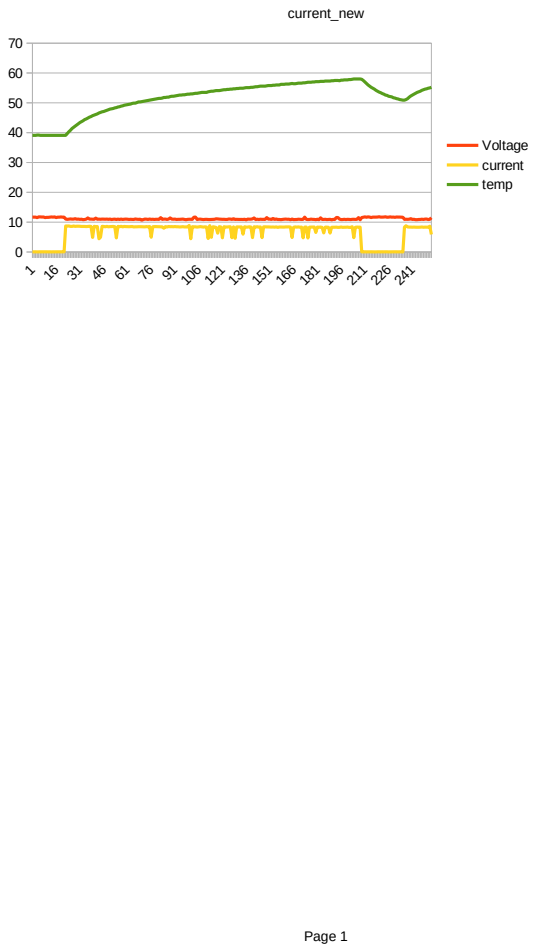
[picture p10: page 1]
current_new; Voltage current temp

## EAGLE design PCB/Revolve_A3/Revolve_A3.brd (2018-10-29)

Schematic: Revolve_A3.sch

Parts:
C1, C2, C4, C5, C6, C8, C10, C12, C13, C15, C16, C18, C19, C20, C21, C23, C24, C27, C28, C29, C30, C31, C32, C35, C38, C40, C43, C44, C53, C54, C56, C60, C61, C63, C64, C66, C67, C69, C70, C72, C73, C74, C82, C83, C84, C85, C87, C99, C107, C108, C110, C114, C115, C133, C134, C138, C140, C141, C142, C150, C151, C155: 0.1uF; C0402; MPN CL10B104KB8NNND
C3, C7, C9, C11, C39, C88, C132: 22nF; C0402; MPN C1005X7R1E223K050BB
C14, C17, C48, C80: 22uF; C1206; MPN CL31B106KAHNNNE
C22, C57, C58, C59, C102: 4.7nF; C0402; MPN CL05B472KA5NNNC
C25: 100uF; 153CLV-0605; MPN RSL0J101MCN1GB
C26, C33, C37, C45, C46, C49, C55, C65, C68, C86, C103: 4.7uF; C0402; MPN GRM155R60J475ME47D
C34, C109, C111, C112, C113: 2.2uF; C0402; MPN GRM155R61A225KE95D
C36, C146, C147, C148, C149, C156, C157: 18pF; C0402; MPN GRM0335C1E180JA01D
C41, C47, C89, C91, C92, C93, C100: 10uF,35V; C0805; MPN GRM21BR6YA106KE43K
C42, C94, C95, C97, C98, C101: 100uF,35V,0.025R; RHS1V10MCN1GS; MPN RHS1V101MCN1GS
C135, C143: 10uF,3.3V; C0805; MPN C0805C106K8PACTU
C136: 470pF; C0402; MPN CL05B471KB5NNNC
D1, D2, D3, D4, D5: MBRA340T3; SMA; MPN MBRA340T3G
EEPROM_WP: TPB1,27; B1,27
IC1, IC6, IC7: 74AHC1G126DCK; SC70-5; MPN M74VHC1GT126DF1G
IC2: CY7C65632; QFN28; MPN CY7C65632-28LTXCT
IC29: LAN8710A; 32-QFN; MPN LAN8710A-EZC-TR
IC30: MTFC2GMDEA; WFBGA; MPN EMMC04G-M627-X03R
J1: CTI-JTAG
J2, J3: 4P-2.0; HW4-2.0; MPN 1125S-4P
JP1, JP2: FIDUCIAL1X2.5; FIDUCIAL-1X2.5
L1: 15uH; NR8040T330; MPN NRS8040T150MJGJ
L2, L3: 150OHM,800mA; L2012C; MPN MU2029-151Y
LED0, LED1, LED2, LED3, LED4, LED5, LED6, LED7, LED8, LED9, LED10, LED11, LED12, LED13: blue; CHIP-LED0603; MPN 19-217/BHC-ZL1M2RY/3T
LOGO1: OSHW_LOGO_FILLX0200-NT; OSHW_FILLX200_NOTEXT
MGT1, MGT2, MGT3, MGT4: MOUNTING_HOLE
PMIC_NRESET: TPTP10R; TP10R
Q1, Q2, Q3, Q8: AON6758; 8-DFN-EP-(5X6); MPN SIRA34DP-T1-GE3
Q4, Q5, Q6, Q7, Q12: NPN-TRANSISTOR_SOT23; SOT23; MPN AO7400
Q9: MMBT2907; SOT23-BEC; MPN MMBT2907ALT3G
Q10, Q11, Q13, Q14: DMC2038LVT; TSOT26; MPN DMC2038LVT-7
R1, R2, R6, R27, R31, R35, R37, R38, R39, R40, R43, R50, R55, R56, R57, R58, R60, R73, R78, R81, R88, R90, R94, R121, R127, R128, R129, R130, R131, R132, R133, R134, R135, R136, R137, R140, R141, R147, R152: 10K,1%; R0402; MPN RC0402FR-0710KL
R3, R4, R7, R8, R9, R10, R11, R29, R30, R42, R138, R139, R149: 0.1R; R0805; MPN RL1220S-R10-F
R5, R13, R14, R15, R16, R17, R18, R19, R20, R21, R23, R24, R25, R28, R32, R33, R34, R36, R44, R46, R47, R48, R51, R54, R61, R62, R63, R64, R65, R66, R67, R68, R69, R74, R75, R76, R77, R89, R91, R92, R93, R112, R142, R143, R144, R145, R171, R172, R173: 4.7K,1%; R0402; MPN RC0402FR-074K7L
R12, R45, R84, R87, R105, R107, R108, R114, R115, R116, R117, R118, R119, R120, R174, R175, R176, R177, R178, R179: 100K,1%; R0402; MPN RC0402FR-07100KL
R22: 13.3K,1%; R0402; MPN RC0402FR-0713K3L
R26: 0.001,1%; R1206; MPN CSR1206-0R001F1
R41, R86, R148: 40.2K,1%; R0402; MPN RC0402FR-0740K2L
R49: 499; R0402; MPN RC0402FR-07499RL
R52, R59, R70, R71, R72, R126: 2.2R; R0402; MPN RC0402FR-072R2L
R53, R106, R109, R110, R111, R153, R154, R155: 1K,1%; R0402; MPN RC0402FR-071KL
R79, R80: 470; R0402; MPN RC0402JR-07470RL
R82: 12.1K, 1%; R0402; MPN RC0402FR-0712K1L
R83: 10,1%; R0402; MPN RC0402FR-0710RL
R85, R95, R96, R97, R98, R99, R100, R101, R102, R103, R104, R161, R162, R180, R181: 100; R0402; MPN RC0402FR-07100RL
R113: 649,1%; R0402; MPN RC0402FR-07649RL
R122, R123, R124, R125: 49.9,1%; R0402; MPN RC0402FR-0749R9L
R146: 47k,NTC; R0402; MPN NCP15WB473E03RC
R150: 1M; R0402; MPN RC0402JR-071ML
R151: 0,DNP; R0402; MPN RC0402FR-071KL
SV1, SV5: MA04-1
SV4, SV6: MA05-2
SYS_5V: TPTP06R; TP06R
SYS_RTC_1V8: TPB1,27; B1,27
SYS_VDD1_3V3: TPTP10R; TP10R
SYS_VDD2_3V3: TPTP11R; TP11R
SYS_VDD3_3V3: TPB1,27; B1,27
U1: OSD3358-512M-BSM; OSD335X-BGA-256; MPN OSD3358-512M-BSM
U3: TPS2061D; SOIC127P600X175-8N
U4, U6, U8, U9, U10: TPD4S012_DRY_6_P1_P; DRY6; MPN TPD4S012DRYR
U5: UA78L05ACD; SOIC127P600X175-8N; MPN UA78L12ACDR
U7: TLVH431; SOT23-3; MPN TLVH431IDBZR
U11: SN74AHC595PW; SOP65P640X120-16N
U12: APX811SOT; SOT143-R; MPN APX811-31UG-7
U13: INA199A1DCKR; SOT65P210X110-6N
U19: CD4050BD; SOIC127P600X175-16N; MPN CD4050BDR
U$2, U$9, U$13, U$14, U$15, U$16: TRINAMIC_TMC2130_QFN36; TRINAMIC_QFN36; MPN TMC2130-LA-T
U$3: LPJ0011BBNL; MPN LPJ0011BBNL
U$4: CC-BY-SA
U$5, U$6: USB-A; MPN 320010475
U$7: TDA19988BHN/C1,557; SOT804-4; MPN TDA19988BHN/C1,518
U$8: USB-MICRO; MPN ST-USB-001G-4
U$10: TPS54202; SOT23; MPN TPS54202DDCR
U$11, U$17: SISS27DN; POWERPAK-1212-8S; MPN SISS27DN-T1-GE3
U$18: TPD12S016-RKT; R-PDSO-G24; MPN TPD12S016PWR
U$19, U$20, U$21: TACT_SWITCH; DHT-1147
U$22: 445C33D24M000003.2X2.5; 403C35E12M00000; MPN ABM8G-12.000MHZ-4Y-T3
VDDS_DDR: TPTP10R; TP10R
VDDS_PLL: TPTP11R; TP11R
VDD_CODE: TPTP10R; TP10R
VDD_MPU: TPTP11R; TP11R
X1, X7, X8, X10, X11, X13, X19, X22, X29: 22-05-7038-03; 7395-03; MPN 640455-3
X2, X20: MSTBA4; MPN 39532-1004
X3, X21, X26: MSTBA2; MPN 39532-1002
X4, X5, X6, X9: 22-05-7028-02; 7395-02; MPN 640455-2
X12, X14, X15, X16, X17, X18, X25: 22-05-7048-04; 7395-04; MPN 640455-4
X24: HDMI4; HDMI-A-TH; MPN 609-4614-2-ND
Y1, Y2: 25MHz; 445C33D24M00000; MPN 445C33D25M00000

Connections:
5VIN_Y: C72.1, R59.2, U$13.26 (VCC)
5VOUT_A: C55.2, R72.1, R73.2, U$16.25 (5VOUT)
5VOUT_E: C65.2, R35.2, R71.1, U$14.25 (5VOUT)
5VOUT_H: C68.2, R31.2, R52.1, U$15.25 (5VOUT)
5VOUT_X: C86.2, R126.1, R140.2, U$2.25 (5VOUT)
5VOUT_Y: C33.2, R37.2, R59.1, U$13.25 (5VOUT)
5VOUT_Z: C37.2, R27.2, R70.1, U$9.25 (5VOUT)
+5V: C36.2, C48.1, C80.1, L1.P$1, R12.1, U1.P10 (VIN_AC), U1.R10 (VIN_AC), U1.T10 (VIN_AC)
+12V: C5.2, U5.1 (OUT), X12.4
+24V: C4.1, C6.2, C8.1, C10.1, C15.1, C16.1, C28.2, C32.2, C35.2, C38.2, C40.1, C41.1, C42.+, C54.2, C56.2, C64.2, C66.2, C67.2, C69.2, C85.2, C89.1, C91.1, C92.1, C93.1, C94.+, C95.+, C97.+, C98.+, C99.2, C100.1, C101.+, D1.C, D2.C, D3.C, D4.C, R26.1, SV4.9, SV6.9, U5.8 (IN), U13.5 (IN-), U$2.16 (VS), U$2.30 (VSA), U$2.31 (VS), U$9.16 (VS), U$9.30 (VSA), U$9.31 (VS), U$13.16 (VS), U$13.30 (VSA), U$13.31 (VS), U$14.16 (VS), U$14.30 (VSA), U$14.31 (VS), U$15.16 (VS), U$15.30 (VSA), U$15.31 (VS), U$16.16 (VS), U$16.30 (VSA), U$16.31 (VS), X3.1, X4.1, X5.1, X6.1, X9.1, X20.1, X20.2, X21.1, X26.1
+24V_FOR_5V: C1.2, C47.1, D5.C, R151.1, U$10.3 (VIN)
A7-RFU-V5: IC30.A7 (NC)
CGND: MGT1.P$1, MGT2.P$1, MGT3.P$1, MGT4.P$1, R149.2, U$3.SHD1, U$3.SHD2, U$5.A9 (SHD1), U$5.A10 (SHD2), U$5.A11 (SHD3), U$5.A12 (SHD4), U$6.A9 (SHD1), U$6.A10 (SHD2), U$6.A11 (SHD3), U$6.A12 (SHD4), U$8.P$6 (GND), U$8.P$7 (GND), U$8.P$8 (GND), U$8.P$9 (GND), U$8.P$10 (GND), U$8.P$11 (GND), X24.P$1 (GND), X24.P$2 (GND), X24.P$3 (GND), X24.P$4 (GND)
DIR_A: U1.A16 (MMC0_DAT0), U$16.7 (REFR_DIR)
DIR_B: SV6.5, U1.B15 (MMC0_CLK)
DIR_C: SV4.5, U1.R6 (GPMC_AD13)
DIR_E: U1.C4 (MCASP0_AHCLKX), U$14.7 (REFR_DIR)
DIR_H: U1.C16 (MMC0_DAT2), U$15.7 (REFR_DIR)
DIR_X: U1.A2 (MCASP0_FSX), U$2.7 (REFR_DIR)
DIR_Y: U1.B1 (MCASP0_AHCLKR), U$13.7 (REFR_DIR)
DIR_Z: U1.B3 (MCASP0_FSR), U$9.7 (REFR_DIR)
DVI_+5V: C21.1, U$18.P$13 (5V_OUT), X24.18 (+5V)
E5-RFU-V5: IC30.E5 (NC)
EEPROM_WP: EEPROM_WP.TP, U1.M2 (EEPROM_WP)
EMMC_RST: IC30.K5 (RST_N), R137.1, U1.B4 (XDMA_EVENT_INTR1)
EMMV_VCCI: C138.1, IC30.C2 (VDDIM)
EMU0: J1.13 (EMU0), R171.2, U1.E2 (EMU0)
EMU1: J1.14 (EMU1), R172.2, U1.E3 (EMU1)
ENABLE_B: SV6.3, U11.6 (QG)
ENABLE_C: SV4.3, U11.7 (QH)
ENABLE_STUFF: Q12.1 (B), R91.1, R112.2, U1.J15 (USB0_DRVVBUS)
END_STOP_X1: U1.N14 (GPMC_BEN1), U19.2 (G=A)
END_STOP_X2: U1.R12 (GPMC_A1), U19.10 (J=D)
END_STOP_X_1_IN: R61.1, U19.3 (A), X22.1
END_STOP_X_2_IN: IC6.4 (O), R64.1, U19.9 (D), X10.1
END_STOP_Y1: U1.T16 (GPMC_A11), U19.4 (H=B)
END_STOP_Y2: U1.P3 (GPMC_CSN0), U19.12 (K=E)
END_STOP_Y_1_IN: R62.1, U19.5 (B), X1.1
END_STOP_Y_2_IN: IC7.4 (O), R65.1, U19.11 (E), X19.1
END_STOP_Z1: U1.T6 (GPMC_AD14), U19.6 (I=C)
END_STOP_Z2: U1.P7 (GPMC_AD15), U19.15 (L=F)
END_STOP_Z_1_IN: R63.1, U19.7 (C), X13.1
END_STOP_Z_2_IN: R66.1, U19.14 (F), X12.1
EN_TK_A: Q14.1 (G1), Q14.3 (G2), R142.2, U11.3 (QD), X11.1
EN_TK_E: Q10.1 (G1), Q10.3 (G2), R76.2, U11.15 (QA), X29.1
EN_TK_H: Q11.1 (G1), Q11.3 (G2), R92.2, U11.1 (QB), X7.1
EN_TK_HBP: Q13.1 (G1), Q13.3 (G2), R93.2, U11.2 (QC), X8.1
FAN0: Q6.1 (B), R25.2, R34.2, U1.P12 (GPMC_A2)
FAN1: Q7.1 (B), R19.2, R33.2, U1.T13 (GPMC_A3)
FAN2: Q4.1 (B), R20.2, R32.2, U1.T4 (GPMC_AD8)
FAN3: Q5.1 (B), R5.2, R21.2, U1.P5 (GPMC_AD9)
FAULT_A: R44.1, U1.R5 (GPMC_AD10), U$16.20 (SWN_DIAG0), U$16.21 (SWP_DIAG1)
FAULT_E: R36.1, U1.T7 (GPMC_CLK), U$14.20 (SWN_DIAG0), U$14.21 (SWP_DIAG1)
FAULT_H: R51.1, U1.J14 (RMII1_REF_CLK), U$15.20 (SWN_DIAG0), U$15.21 (SWP_DIAG1)
FAULT_X: R143.2, U1.T5 (GPMC_AD11), U$2.20 (SWN_DIAG0), U$2.21 (SWP_DIAG1)
FAULT_Y: R144.2, U1.R7 (GPMC_CSN3), U$13.20 (SWN_DIAG0), U$13.21 (SWP_DIAG1)
FAULT_Z: R28.1, U1.T12 (GPMC_A0), U$9.20 (SWN_DIAG0), U$9.21 (SWP_DIAG1)
GANG: IC2.23 (GANG), R87.2
GND: C1.1, C4.2, C5.1, C6.1, C8.2, C10.2, C12.2, C13.2, C14.2, C15.2, C16.2, C17.2, C18.1, C19.2, C20.1, C21.2, C23.2, C24.2, C25.-, C26.2, C27.2, C28.1, C29.2, C30.2, C31.2, C32.1, C33.1, C34.2, C37.1, C40.2, C41.2, C42.-, C43.2, C44.2, C45.2, C46.2, C47.2, C48.2, C49.2, C53.2, C54.1, C55.1, C57.2, C58.2, C59.2, C60.2, C61.2, C63.2, C64.1, C65.1, C67.1, C68.1, C70.2, C72.2, C73.2, C74.2, C80.2, C82.2, C83.2, C84.2, C85.1, C86.1, C87.2, C89.2, C91.2, C92.2, C93.2, C94.-, C95.-, C97.-, C98.-, C100.2, C101.-, C102.2, C103.2, C108.2, C109.2, C110.2, C111.2, C112.2, C113.2, C114.2, C115.2, C132.2, C133.2, C134.2, C135.2, C136.2, C138.2, C140.2, C141.2, C142.2, C143.2, C148.2, C149.2, C150.2, C155.2, C156.1, C157.1, IC1.3 (GND), IC2.18 (I2C_SCL), IC2.29 (PAD), IC6.3 (GND), IC7.3 (GND), IC29.33 (GND_EP), IC30.A6 (NC), IC30.C4 (VSSQ), IC30.E7 (VSS), IC30.G5 (VSS), IC30.H10 (VSS), IC30.K8 (VSS), IC30.N2 (VSSQ), IC30.N5 (VSSQ), IC30.P4 (VSSQ), IC30.P6 (VSSQ), J1.4 (TDIS), J1.8 (GND1), J1.10 (GND2), J1.12 (GND3), J1.16 (GND4), J1.20 (GND5), J2.4, J3.4, LED0.C, LED1.C, LED2.C, LED3.C, LED4.C, LED5.C, LED6.C, LED7.C, LED8.C, LED9.C, LED10.C, LED11.C, LED12.C, LED13.C, Q1.1 (S), Q1.2 (S), Q1.3 (S), Q2.1 (S), Q2.2 (S), Q2.3 (S), Q3.1 (S), Q3.2 (S), Q3.3 (S), Q4.2 (E), Q5.2 (E), Q6.2 (E), Q7.2 (E), Q8.1 (S), Q8.2 (S), Q8.3 (S), Q10.5 (S1), Q11.5 (S1), Q12.2 (E), Q13.5 (S1), Q14.5 (S1), R3.1, R4.1, R5.1, R6.1, R7.1, R8.1, R9.1, R10.1, R11.1, R22.2, R29.1, R30.1, R32.1, R33.1, R34.1, R42.1, R43.1, R46.1, R47.1, R48.1, R50.1, R53.2, R54.2, R58.1, R60.1, R75.1, R76.1, R79.2, R80.2, R81.1, R82.1, R90.2, R91.2, R92.1, R93.1, R94.2, R106.1, R107.1, R108.1, R109.1, R110.1, R111.1, R113.2, R114.2, R115.1, R116.1, R117.2, R121.2, R138.1, R139.1, R141.1, R142.1, R146.2, R148.2, R149.1, R152.2, R173.2, R174.1, R175.1, R176.1, R177.1, R178.1, R179.1, SV1.1, SV4.1, SV5.1, SV6.1, U1.D8 (DGND), U1.D9 (DGND), U1.E5 (DGND), U1.E6 (DGND), U1.E7 (DGND), U1.E8 (DGND), U1.E9 (DGND), U1.E10 (DGND), U1.E11 (DGND), U1.E12 (DGND), U1.F5 (DGND), U1.F12 (DGND), U1.G5 (DGND), U1.G12 (DGND), U1.H4 (DGND), U1.H5 (DGND), U1.H12 (DGND), U1.H13 (DGND), U1.J4 (DGND), U1.J5 (DGND), U1.J12 (DGND), U1.J13 (DGND), U1.K5 (DGND), U1.K12 (DGND), U1.L5 (DGND), U1.L12 (DGND), U1.L14 (USB1_ID), U1.M5 (DGND), U1.M6 (DGND), U1.M7 (DGND), U1.M8 (DGND), U1.M9 (DGND), U1.M10 (DGND), U1.M11 (DGND), U1.M12 (DGND), U1.N8 (DGND), U1.N9 (DGND), U3.1 (GND), U4.4 (GND), U5.2 (COM_2), U5.3 (COM_3), U5.6 (COM_4), U5.7 (COM), U6.4 (GND), U8.4 (GND), U9.4 (GND), U10.4 (GND), U11.8 (GND), U11.13 (~OE), U12.1 (GND), U13.1 (REF), U13.2 (GND), U19.8 (VSS), U$2.1 (CLK), U$2.11 (GND), U$2.12 (GND), U$2.17 (ENCN_DCO), U$2.22 (DRV_ENN_CFG6), U$2.24 (GNDA), U$2.35 (GND), U$2.36 (TST_MODE), U$2.GND_PAD (GND), U$3.8 (GND), U$5.4 (GND), U$5.8 (GND), U$6.4 (GND), U$6.8 (GND), U$7.8 (VPB[1]), U$7.9 (VPB[0]), U$7.16 (VPC[2]), U$7.17 (VPC[1]), U$7.18 (VPC[0]), U$7.19 (VPP), U$7.49 (TEST), U$7.53 (A0_I2C), U$7.54 (A1_I2C), U$7.61 (VPA[2]), U$7.62 (VPA[1]), U$7.63 (VPA[0]), U$7.P$1 (GND.PAD), U$8.P$5 (5), U$9.1 (CLK), U$9.11 (GND), U$9.12 (GND), U$9.17 (ENCN_DCO), U$9.22 (DRV_ENN_CFG6), U$9.24 (GNDA), U$9.35 (GND), U$9.36 (TST_MODE), U$9.GND_PAD (GND), U$10.1 (GND), U$13.1 (CLK), U$13.11 (GND), U$13.12 (GND), U$13.17 (ENCN_DCO), U$13.22 (DRV_ENN_CFG6), U$13.24 (GNDA), U$13.35 (GND), U$13.36 (TST_MODE), U$13.GND_PAD (GND), U$14.1 (CLK), U$14.11 (GND), U$14.12 (GND), U$14.17 (ENCN_DCO), U$14.22 (DRV_ENN_CFG6), U$14.24 (GNDA), U$14.35 (GND), U$14.36 (TST_MODE), U$14.GND_PAD (GND), U$15.1 (CLK), U$15.11 (GND), U$15.12 (GND), U$15.17 (ENCN_DCO), U$15.22 (DRV_ENN_CFG6), U$15.24 (GNDA), U$15.35 (GND), U$15.36 (TST_MODE), U$15.GND_PAD (GND), U$16.1 (CLK), U$16.11 (GND), U$16.12 (GND), U$16.17 (ENCN_DCO), U$16.22 (DRV_ENN_CFG6), U$16.24 (GNDA), U$16.35 (GND), U$16.36 (TST_MODE), U$16.GND_PAD (GND), U$18.P$6 (GND), U$18.P$14 (GND), U$18.P$19 (GND), U$19.2, U$20.4, U$21.4, X1.2, X2.1, X2.2, X7.3, X8.3, X10.2, X11.3, X12.2, X13.2, X19.2, X22.2, X24.2 (TMDS_DATA2_SHIELD), X24.5 (TMDS_DATA1_SHIELD), X24.8 (TMDS_DATA0_SHIELD), X24.11 (TMDS_CLOCK_SHIELD), X24.17 (DDC/CEC-GRND), X29.3
GNDA_ADC: C22.2, C107.2, C151.2, U1.A9 (AGND_ADC), U1.B9 (VREFN)
HDMI_1V8: C12.1, C29.1, C31.1, C108.1, C109.1, C110.1, C111.1, C112.1, C113.1, C114.1, C115.1, L3.1, U$7.5 (VDDDC1), U$7.14 (VDDD1(IO)(1V8)), U$7.29 (VDDDC2), U$7.35 (VDDA(1V8)), U$7.36 (VDDA3(TX)(1V8)), U$7.41 (VDDA2(TX)(1V8)), U$7.46 (VDDA1(TX)(1V8)), U$7.47 (VDDA1(PLL)(1V8)), U$7.48 (VDDA2(PLL)(1V8)), U$7.55 (VDDD2(IO)(1V8))
HDMI_HPD: U$7.31 (HPD), U$18.P$4 (HPD_A), U$18.P$5 (LS_OE)
HDMI_INT: U1.R15 (GPMC_A10), U$7.50 (INT)
HEATER_A: R74.2, R75.2, R181.2, U1.N1 (GPMC_OEN_REN)
HEATER_E: R15.2, R47.2, R161.2, U1.M1 (GPMC_ADVN_ALE)
HEATER_H: R14.2, R48.2, R162.2, U1.N3 (GPMC_BEN0_CLE)
HEATER_HBP: R16.2, R46.2, R180.2, U1.N2 (GPMC_WEN)
I2C0_SCL: U1.C10 (I2C0_SCL), U1.D10 (PMIC_SCL), U$7.52 (CSCL)
I2C0_SDA: U1.C11 (I2C0_SDA), U1.D11 (PMIC_SDA), U$7.51 (CSDA)
I2C1_SCL: J2.1, U1.B11 (UART1_TXD)
I2C1_SDA: J2.2, U1.A11 (UART1_RXD)
IREF_E: R35.1, R60.2, U$14.23 (AIN_IREF)
IREF_H: R31.1, R50.2, U$15.23 (AIN_IREF)
IREF_X: R140.1, R141.2, U$2.23 (AIN_IREF)
IREF_Y: R6.2, R37.1, U$13.23 (AIN_IREF)
IREF_Z: R27.1, R58.2, U$9.23 (AIN_IREF)
I_MEASURE: U1.C9 (AIN6), U13.6 (OUT)
LCD_D0: R116.2, U1.G3 (LCD_DATA0), U$7.15 (VPC[3])
LCD_D1: R115.2, U1.G2 (LCD_DATA1), U$7.13 (VPC[4])
LCD_D2: R120.1, U1.G1 (LCD_DATA2), U$7.12 (VPC[5])
LCD_D3: R119.1, U1.H3 (LCD_DATA3), U$7.11 (VPC[6])
LCD_D4: R118.1, U1.H2 (LCD_DATA4), U$7.10 (VPC[7]), U$21.2
LCD_D5: R117.1, U1.H1 (LCD_DATA5), U$7.7 (VPB[2])
LCD_D6: R179.2, U1.J3 (LCD_DATA6), U$7.6 (VPB[3])
LCD_D7: R178.2, U1.J2 (LCD_DATA7), U$7.3 (VPB[4])
LCD_D8: R177.2, U1.J1 (LCD_DATA8), U$7.2 (VPB[5])
LCD_D9: R176.2, U1.K3 (LCD_DATA9), U$7.1 (VPB[6])
LCD_D10: R175.2, U1.K2 (LCD_DATA10), U$7.64 (VPB[7])
LCD_D11: R174.2, U1.K1 (LCD_DATA11), U$7.60 (VPA[3])
LCD_D12: R108.2, U1.L3 (LCD_DATA12), U$7.59 (VPA[4])
LCD_D13: R107.2, U1.L2 (LCD_DATA13), U$7.58 (VPA[5])
LCD_D14: R114.1, U1.L1 (LCD_DATA14), U$7.57 (VPA[6])
LCD_D15: R105.2, U1.M3 (LCD_DATA15), U$7.56 (VPA[7])
LCD_DE: U1.E1 (LCD_AC_BIAS_EN), U$7.20 (DE/FREF)
LCD_HSYNC: U1.F2 (LCD_HSYNC), U$7.22 (HSYNC/HREF)
LCD_PCLK: U1.F1 (LCD_PCLK), U$7.4 (PCLK)
LCD_VSYNC: U1.F3 (LCD_VSYNC), U$7.21 (VSYNC/VREF)
MDIO_CLK: IC29.17 (MDC), U1.D13 (MDC)
MDIO_DATA: IC29.16 (MDIO), R85.2, U1.E13 (MDIO)
MII1_COL: R103.2, U1.F15 (MII1_COL)
MII1_CRS_DV: R104.2, U1.F14 (MII1_CRS)
MII1_RXCLK: R100.2, U1.E16 (MII1_RX_CLK)
MII1_RXD0: R99.2, U1.E14 (MII1_RXD0)
MII1_RXD1: R97.2, U1.D16 (MII1_RXD1)
MII1_RXD2: R96.2, U1.D15 (MII1_RXD2)
MII1_RXD3: R95.2, U1.D14 (MII1_RXD3)
MII1_RXDV: R98.2, U1.F16 (MII1_RX_DV)
MII1_RXERR: R101.2, U1.E15 (MII1_RX_ER)
MII1_TXCLK: R102.2, U1.H16 (MII1_TX_CLK)
MII1_TXD0: IC29.22 (TXD0), U1.H15 (MII1_TXD0)
MII1_TXD1: IC29.23 (TXD1), U1.H14 (MII1_TXD1)
MII1_TXD2: IC29.24 (TXD2), U1.G16 (MII1_TXD2)
MII1_TXD3: IC29.25 (TXD3), U1.G15 (MII1_TXD3)
MII1_TXEN: IC29.21 (TXEN), U1.G14 (MII1_TX_EN)
MMC1_CLK: IC30.M6 (CLK), R136.1, U1.P2 (GPMC_CSN1)
MMC1_CMD: IC30.M5 (CMD), R135.1, U1.P1 (GPMC_CSN2)
MMC1_DAT0: IC30.A3 (DAT0), R127.1, U1.R3 (GPMC_AD0)
MMC1_DAT1: IC30.A4 (DAT1), R128.1, U1.R2 (GPMC_AD1)
MMC1_DAT2: IC30.A5 (DAT2), R129.1, U1.R1 (GPMC_AD2)
MMC1_DAT3: IC30.B2 (DAT3), R130.1, U1.T3 (GPMC_AD3)
MMC1_DAT4: IC30.B3 (DAT4), R131.1, U1.T2 (GPMC_AD4)
MMC1_DAT5: IC30.B4 (DAT5), R132.1, U1.T1 (GPMC_AD5)
MMC1_DAT6: IC30.B5 (DAT6), R133.1, U1.P4 (GPMC_AD6)
MMC1_DAT7: IC30.B6 (DAT7), R134.1, U1.R4 (GPMC_AD7)
MODE2: IC29.15 (COL/CRS_DV/MODE2), R103.1, R155.2
unnamed: R41.1, R88.2, U7.1 (REF)
unnamed: U$13.13 (OB1), X15.3
unnamed: C3.2, U$13.27 (CPO)
unnamed: Q9.B, R49.2, U7.2 (CATHODE)
unnamed: C2.2, U$10.6 (BOOT)
unnamed: U$9.34 (OA1), X16.1
unnamed: Q12.3 (C), R86.2
unnamed: LED5.A, R19.1
unnamed: Q6.3 (C), X9.2
unnamed: C9.2, U$15.27 (CPO)
unnamed: R9.2, U$15.14 (BRB)
unnamed: C7.2, U$9.27 (CPO)
unnamed: R7.2, U$9.14 (BRB)
unnamed: U$9.32 (OA2), X16.2
unnamed: R24.2, R53.1, U$17.G
unnamed: IC2.8 (RREF), R113.1
unnamed: U$13.32 (OA2), X15.2
unnamed: U$13.34 (OA1), X15.1
unnamed: LED0.A, R25.1
unnamed: U$14.34 (OA1), X17.1
unnamed: C36.1, R12.2, R22.1, U$10.4 (FB)
unnamed: R8.2, U$9.33 (BRA)
unnamed: Q5.3 (C), X6.2
unnamed: R84.2, R86.1, U$11.G
unnamed: C7.1, U$9.28 (CPI)
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

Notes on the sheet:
Fan drivers
Power in
5V step down converter
MOSFET E
MOSFET HBP
MOSFET H
End stops 2
Thermistors
End stops 1
MOSFET A
RESET
POWER
McASP is disabled.
USB
LAN
HDMI
FANS+End stops
PWM etc
Power
eMMC
STP H/A
STP Z/E
STP X/Y
SIP LCD + LAN
Ext driver B
Ext driver C
Analog etc
R151 can be populated with 0R if TPS54202H is used instead of TPS54202

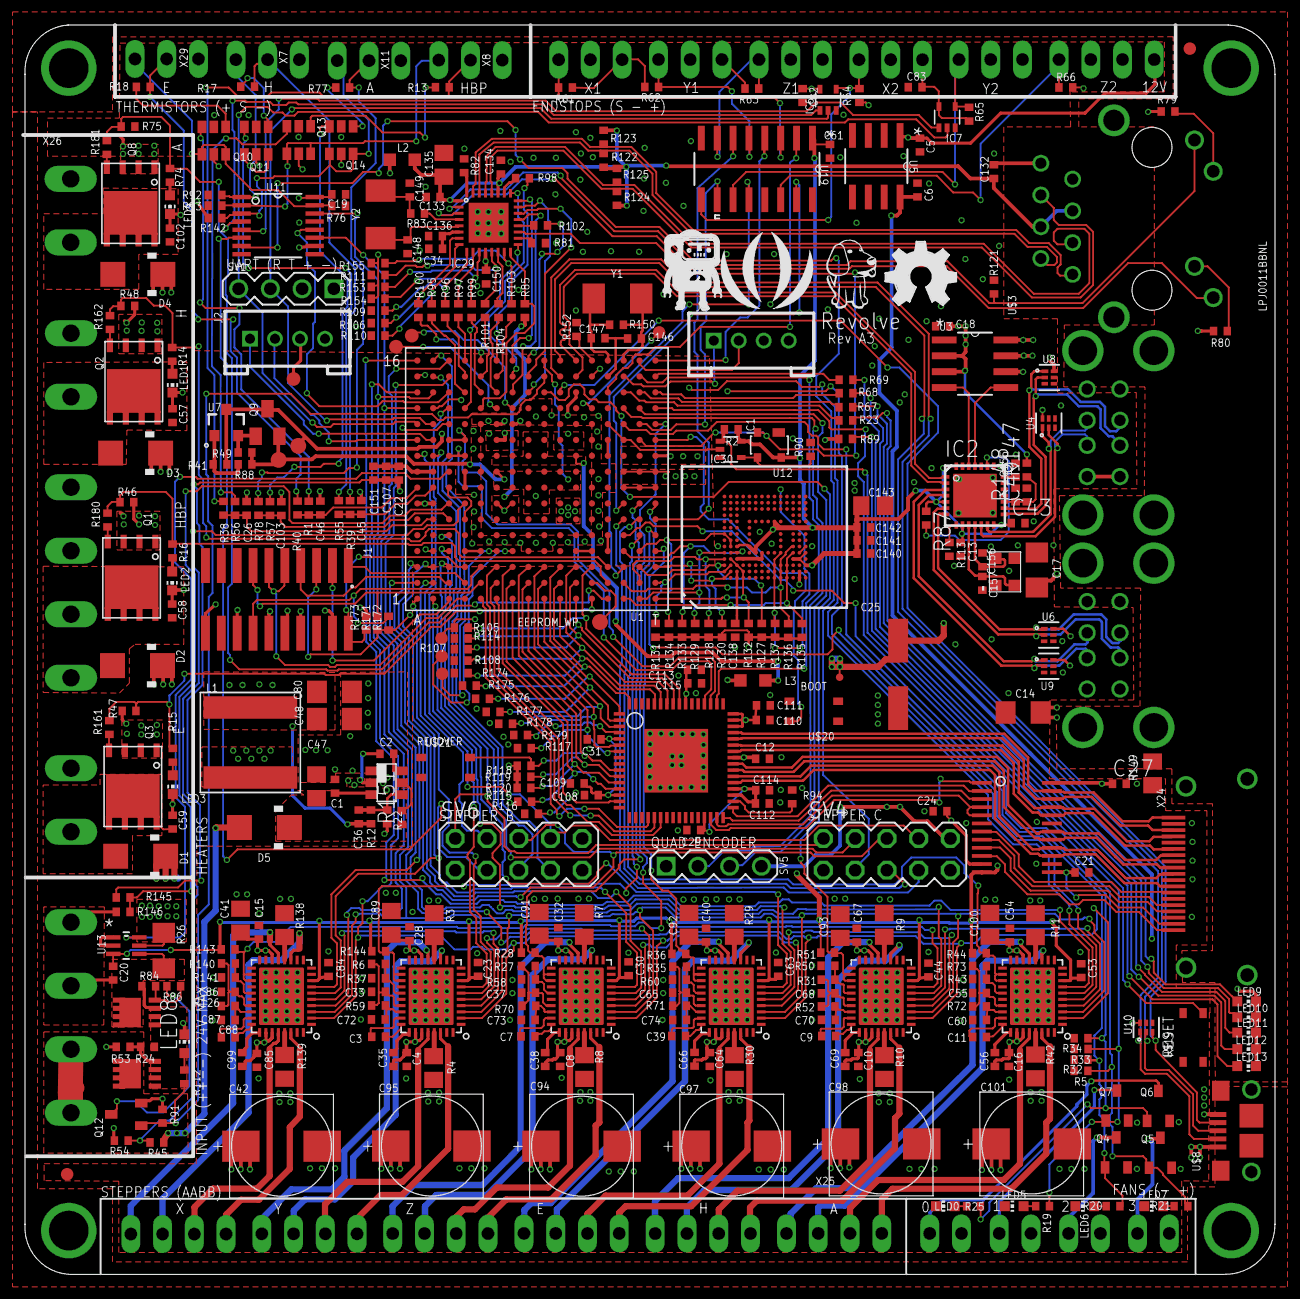
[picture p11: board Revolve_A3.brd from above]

Board: 4 copper layers, 100.0 x 100.0 mm, 417 parts (0 on the bottom side), 367 nets.

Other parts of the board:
U$1: LOGO_BIG
U$12: BB-LOGO
U$23: S_LOGO

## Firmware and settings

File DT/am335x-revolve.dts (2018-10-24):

/*
 * Copyright (C) 2012 Texas Instruments Incorporated - http://www.ti.com/
 *
 * This program is free software; you can redistribute it and/or modify
 * it under the terms of the GNU General Public License version 2 as
 * published by the Free Software Foundation.
 */
/dts-v1/;

#include "am33xx.dtsi"
/* #include "am335x-bone-jtag.dtsi" */

/ {

	model = "Revolve:00A0";
	compatible = "ti,am335x-bone-black", "ti,am335x-bone", "ti,am33xx";

	cpus {
		cpu@0 {
			cpu0-supply = <&dcdc2_reg>;
		};
	};

	memory@80000000 {
		device_type = "memory";
		reg = <0x80000000 0x10000000>; /* 256 MB */
	};

	chosen {
		stdout-path = &uart0;
	};

	vmmcsd_fixed: fixedregulator0 {
		compatible = "regulator-fixed";
		regulator-name = "vmmcsd_fixed";
		regulator-min-microvolt = <3300000>;
		regulator-max-microvolt = <3300000>;
	};

    leds {
	    pinctrl-names = "default";
	    pinctrl-0 = <&user_leds_s0>;

	    compatible = "gpio-leds";

	    led1 {
		    label = "beaglebone:green:usr1";
		    gpios = <&gpio1 22 GPIO_ACTIVE_HIGH>;
            trigger-sources = <&usb1>;
		    /*linux,default-trigger = "mmc0";*/
		    default-state = "off";
	    };

	    led2 {
		    label = "beaglebone:green:usr2";
		    gpios = <&gpio1 23 GPIO_ACTIVE_HIGH>;
		    linux,default-trigger = "cpu0";
		    default-state = "off";
	    };

	    led3 {
		    label = "beaglebone:green:usr3";
		    gpios = <&gpio1 24 GPIO_ACTIVE_HIGH>;
		    linux,default-trigger = "mmc1";
		    default-state = "off";
	    };
	    led4 {
		    label = "beaglebone:green:usr0";
		    gpios = <&gpio1 25 GPIO_ACTIVE_HIGH>;
		    linux,default-trigger = "heartbeat";
		    default-state = "off";
	    };

    };


    gpio_keys {
        compatible = "gpio-keys";
        pinctrl-names = "default";
        pinctrl-0 = <&end_stop_pins>;
        pinctrl-1 = <&stepper_fault_pins>;
        #address-cells = <1>;
        #size-cells = <0>;

        switch_x1 {
            label               = "Replic:End-stop-X1";
            debounce_interval   = <50>;
            linux,code          = <112>;
            gpios               = <&gpio1 28 0x5>;
            gpio-key,wakeup;
        };				
        switch_x2 {
            label               = "Replic:End-stop-X2";
            debounce_interval   = <50>;
            linux,code          = <113>;
            gpios               = <&gpio1 17 0x5>;
            gpio-key,wakeup;
        };
        switch_y1 {
            label               = "Replic:End-stop-Y1";
            debounce_interval   = <50>;
            linux,code          = <114>;
            gpios               = <&gpio1 27 0x5>;
            gpio-key,wakeup;
        };				
        switch_y2 {
            label               = "Replic:End-stop-Y2";
            debounce_interval   = <50>;
            linux,code          = <115>;
            gpios               = <&gpio1 29 0x5>;
            gpio-key,wakeup;
        };				
        switch_z1 {
            label               = "Replic:End-stop-Z1";
            debounce_interval   = <50>;
            linux,code          = <116>;
            gpios               = <&gpio1 14 0x5>;
            gpio-key,wakeup;
        };				
        switch_z2 {
            label               = "Replic:End-stop-Z2";
            debounce_interval   = <50>;
            linux,code          = <117>;
            gpios               = <&gpio1 15 0x5>;
            gpio-key,wakeup;
        };				
        fault_x {
            label               = "Replic:Fault-X";
            debounce_interval   = <50>;
            linux,code          = <90>;
            gpios               = <&gpio0 27 0x5>;
            gpio-key,wakeup;	
        };
        fault_y {
            label               = "Replic:Fault-Y";
            debounce_interval   = <50>;
            linux,code          = <91>;
            gpios               = <&gpio2 0 0x5>;
            gpio-key,wakeup;	
        };
        fault_z {
            label               = "Replic:Fault-Z";
            debounce_interval   = <50>;
            linux,code          = <92>;
            gpios               = <&gpio1 16 0x5>;
            gpio-key,wakeup;	
        };
        fault_e {
            label               = "Replic:Fault-E";
            debounce_interval   = <50>;
            linux,code          = <93>;
            gpios               = <&gpio2 1 0x5>;
            gpio-key,wakeup;	
        };
        fault_h {
            label               = "Replic:Fault-H";
            debounce_interval   = <50>;
            linux,code          = <94>;
            gpios               = <&gpio0 29 0x5>;
            gpio-key,wakeup;	
        };
        fault_a {
            label               = "Replic:Fault-A";
            debounce_interval   = <50>;
            linux,code          = <94>;
            gpios               = <&gpio0 26 0x5>;
            gpio-key,wakeup;	
        };
    };


    pwm4: pwm-heater-e {
        compatible = "ti,omap-dmtimer-pwm";
        ti,timers = <&timer4>;
        #pwm-cells = <3>;
        pinctrl-names = "default";
	    pinctrl-0 = <&timer4_pins>;	

    };

    pwm5: pwm-heater-h {
        compatible = "ti,omap-dmtimer-pwm";
        ti,timers = <&timer5>;
        #pwm-cells = <3>;
        pinctrl-names = "default";
	    pinctrl-0 = <&timer5_pins>;	

    };

    pwm6: pwm-heater-hbp {
        compatible = "ti,omap-dmtimer-pwm";
        ti,timers = <&timer6>;
        #pwm-cells = <3>;
        pinctrl-names = "default";
	    pinctrl-0 = <&timer6_pins>;	

    };

    pwm7: pwm-heater-a {
        compatible = "ti,omap-dmtimer-pwm";
        ti,timers = <&timer7>;
        #pwm-cells = <3>;
        pinctrl-names = "default";
	    pinctrl-0 = <&timer7_pins>;	

    };
};


&cpu0_opp_table {
	/*
	 * All PG 2.0 silicon may not support 1GHz but some of the early
	 * BeagleBone Blacks have PG 2.0 silicon which is guaranteed
	 * to support 1GHz OPP so enable it for PG 2.0 on this board.
	 */
	oppnitro-1000000000 {
		opp-supported-hw = <0x06 0x0100>;
	};
};
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

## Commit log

2016-11-20 Not finished
    [Revolve_A0.brd, Revolve_A0.sch]
2017-10-03 Starting up work again
    [Pin-mux.ods, Revolve_A0.brd, Revolve_A0.sch]
2017-10-07 Started porting to SIP-SM, changed to TMC2130
    [Revolve_A0.brd, Revolve_A0.sch]
2017-10-08 New Step down, moved some stuff around
    [Revolve_A0.brd, Revolve_A0.sch]
2017-10-14 Working on the LAN layout
    [Revolve_A0.brd, Revolve_A0.sch]
2017-10-18 Working on layout
    [Revolve_A0.brd, Revolve_A0.sch]
2017-10-21 Almost done with schematic
    [Revolve_A0.brd, Revolve_A0.sch]
2017-10-22 Almost done routing. Switched to high side measurement of current
    [Revolve_A0.brd, Revolve_A0.sch]
2017-10-25 Working on DRC errors
    [Revolve_A0.brd, Revolve_A0.sch]
2017-10-25 DRC done, time to start documentation
    [Revolve_A0.brd, Revolve_A0.sch]
2017-10-26 REady for board review
    [Revolve_A0.brd, Revolve_A0.sch]
2017-10-26 Added readme
    [Revolve_A0.brd, Revolve_A0.sch]
2017-10-26 Adde dimages
    [Revolve_A0_bom.xlsx]
2017-10-28 Added calculations on PMOS to readme
    [Revolve_A0.brd, Revolve_A0.sch]
2017-10-31 Ordered PCB and stencil + parts from OSH park/Digi key
    [Revolve_A0.brd, Revolve_A0.csv, Revolve_A0.sch]
2017-12-07 Adding current DT
    [Revolve_A0.csv, Revolve_A0_bom.xlsx]
2018-03-29 Adding rev A1
    [Pin-mux.ods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]
2018-10-24 Uploading Rev A2
    [Revolve_A2.brd, Revolve_A2.sch, Revolve_A2_BoM.csv]
2018-10-29 Adding Rev A3, revision used for first prototype run
    [Revolve_A3.brd, Revolve_A3.csv, Revolve_A3.sch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]
2019-04-18 Added a design with a new input stage. Also added a project for doing spice simulations
    [Revolve_A5-B_Mask.gbs, Revolve_A5-Bottom.gbl, Revolve_A5-Edge_Cuts.gm1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]
2019-06-17 Added files needed for Umikaze.
    [Revolve_A5.sch, Revolve_SPICE.sch, Spice.sch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]
